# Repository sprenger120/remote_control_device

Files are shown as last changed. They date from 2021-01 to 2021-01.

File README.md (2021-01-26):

# remote_control_device

Firmware, KiCAD files, 3D designes of an embedded STM32 based device I was commissioned to create for an autonomous bike. **Clone with --recursive**
It reads receives stick positions from a hobby remote control (FrSky based) and controls various actors around the bike. Also serves as a CANopen bus master, monitoring for timeouts and handling some safety aspects.   
The firmware is fully unit tested and fuzzed using American Fuzzy Lop. 

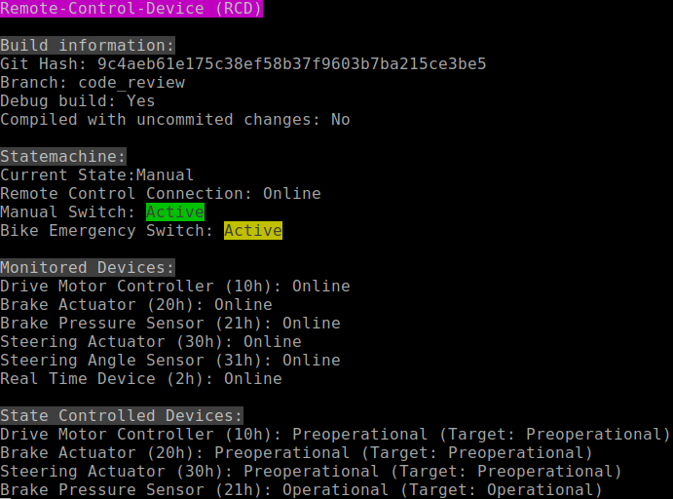
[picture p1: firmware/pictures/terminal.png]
radio front image Serial console


Remote control system for the autonomous bike(s) based on:
 
* FrSky's QX7 remote control
* FrSky's XM+ diversity, non-telemetry receiver
* OpenTX remote control firmware
* ST's NUCLEO-F302R8 board
* custom adapter board
* CANfestival CANopen stack
* STM32 Cube HAL 
* FreeRTOS 

### Project overview / folder stucture
<pre>
remote_control
|-- hardware*          **General information and assembly instructions**
|   |-- 3D             3D models of the units case
|   |-- datasheets     all relevant datasheets of components used in the custom adapter board
|   |-- adapterBoard   KiCAD 5 files
|   |   |-- bom        Interactive BOM for PCB assembly
|-- firmware*          **Code for the micro controller**
</pre>
\* contains extra readme

### General usage of remote control (radio)

Switch on the remote control by holding the center button for 2 seconds. The remote control device in the bike will be in *start* mode until radio link is engaged and all canbus devices area ready. Beware that getting **too close** to the antennas of the RDC with the radio will cause it to loose connection due to overload (the receiver is very sensitive).
The radio will start beeping if left untouched for more than 60 minutes or if the batteries get low. It will never shut off by itself and **will** kill the batteries if signals are ignored.   

To enable any mode the safety switch (momentary - will return to by it's own to default position) has to be flipped up **before** activating either of the two mode switches.
Remote mode will not activate if the throttle is raised. If two modes are activated at the same none will activate.

Emergency can be pressed at at any time. When inside remote or autonomous all switches have to be returned to idle to
leave emergency. Emergency will only be active for the duration of the button press when bike is idling.   

Manual mode overrides **all** control of the bike; even emergency. When exiting manual the bike will not be directly returning to the previous mode.  

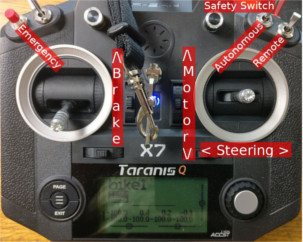
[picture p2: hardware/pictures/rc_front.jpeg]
radio front image


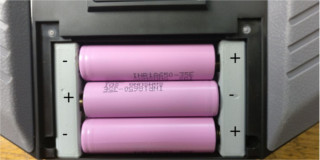
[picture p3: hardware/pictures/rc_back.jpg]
radio back image


### Remote control device LED codes
The LEDs of the device can be in the following states

- off/dim
- fast blinking
- on
- counting (blinking for *n* cycles, off for longer time, repeating)

##### Hardware LED

- off/dim: device is starting
- fast blinking:
    waiting for all canfestival nodes to start up
    no actor values will be sent until this is done
- on: (no errors)
- counting mode:
    - lower counts overwrite higher ones (lower = more important error)
    - 1 count: can network error
    - 2 count: brake heartbeat timeout
    - 3 count: steering timeout
    - 4 count: wheel motor timeout

##### Remote LED

- on: remote control connection established (no errors)
- fast blinking: manual mode (overwrites connection lost / established)
- off: connection lost

### Wiring of remote control device
Input voltage 6-24V (reverse polarity protected) or USB powered through nucleo. ESD protection only rudimentary due to layout error. 
Do not power up device without antennas attached it may shorten the lifespan of the receiver. Switch 01 = manual mode. Switch 02 = hard emergency. Just connect a switch, pull-up is provided by the board.

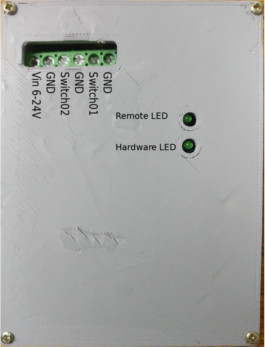
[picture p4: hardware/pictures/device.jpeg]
unit image


## Device pictures

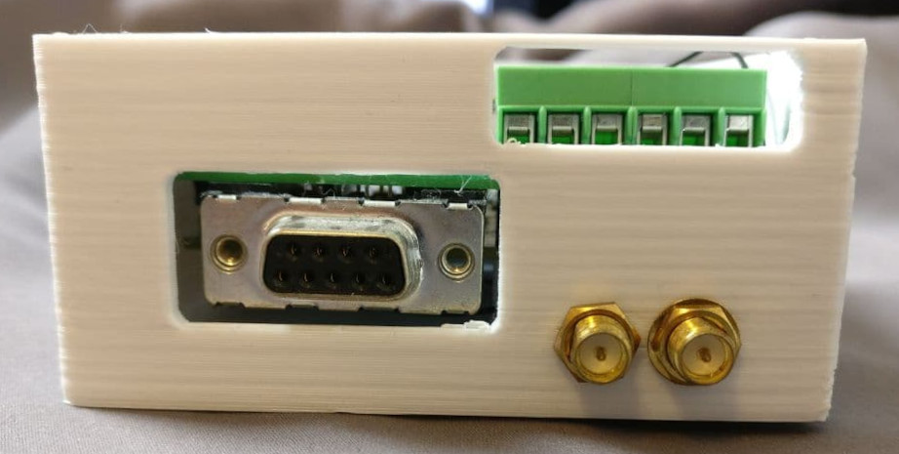
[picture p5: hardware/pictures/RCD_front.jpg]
front image


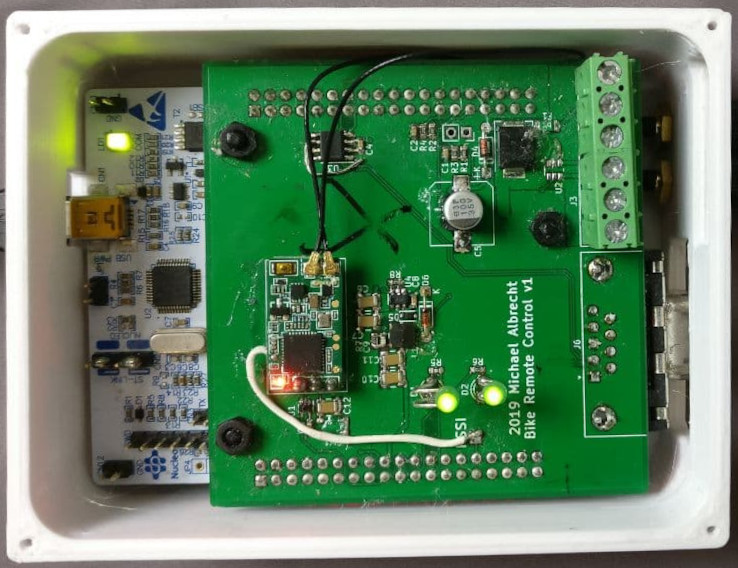
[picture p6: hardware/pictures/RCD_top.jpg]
top without lid


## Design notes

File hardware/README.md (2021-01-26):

# Hardware
- NUCLEO-64 with STM32F302R8 processor with a custom adapter board ontop 
- FrSky XM+ receiver module soldered to the adapter board
- FrSky QX7 remote control with custom emergency stop button and LiIon batteries
- Designed with KiCad 5

### Configuration of remote control
Settings applied to the remote control. You may use OpenTX Companion to copy the config from one radio to the next.

Radio Setup:

- set date, time
- set batt range 9,9-12.6
- batt low warning 10v
- inactivity 60min
- backlight mode: keys
- global functions:
  - 01: on, volume, Input11(s1), active

Setup:

- model name: bike 1
 - s-warning: a,b deactivated
 - internal rf
   - d16
   - ch1-16
   - rx num 1
   - binding:  ch1-8 telem on
   - failsafe: no pulses
- inputs: T, A, E, R, SA, SB, SC, SD, SH, SF, S1, S2, MAX, MAX, MAX, MAX
 - SA input weight -100, offset -100
- mixer click every entry once to assign input
- logical switches
  - 01: a>x, SC, -50
  - 02: a>x, SD, -50
  - 03: AND, L01, L02
- special functions:
  - 01: L03, play sound, wrn1, 1 
  - 02: SA half, play sound, wrn2, -

### Modification of remote control
Opened the unit and removed switch SA and replaced it with a pushbutton. Original hole needs to be enlarged with a drill.

### adapterBoard v1 PCB  Notes
- Buck converter feedback resistive divider component R7 should be 52.3K instead of 52.3R (installed 51K as substitute), corrected in schematic
- XM+ receiver power switch is correctly denoted as normally closed, normally open was accidentally bought, removed SW1 and bridged pads so receiver is always on
- 10uF MLCC were specified as 1210 (imp.) components, 1206 (imp.) were bought, installed 1206 components without issue
- D-SUB connector needs to be soldered to bottom layer because of accidental pinout mirroring
- Modifications to Nucleo board so PCB fits ontop for soldering
   - Snip off Arduino headers on both sides
   - Remove User and Reset button caps and snip button stem even with button casing 
   - Snip off two pin header with jumpers and solder bridges so originl configuration with jumpers is estabilished
- "debugUART" (USART1) and XM+ USART (USART2) need to be switched because the built-in STLinks UART converter is connected to USART2
to achive this the following was done
  - SB14, SB13 resistors have been removed
  - wiring from USART1's pins has been added to the STLinks side of the resistors
- Removed U2 as it is used incorrectly and bridges SW01 and SW02

### Assembly
- assemble adapter board according to interactive bom in adapterBoard/bom
- don't forget to do the buck converter and switch fixes mentioned above
- solder on the XM+ with the help of 3x1 Dupont pin header
- remove original antennas very carefully (do not pull straight up but use a lever below the crimp to pry it off)
- attach the two MHF4 -> RP-SMA adapter cables
- 3D print enclosure (3D folder, [online cad](https://cad.onshape.com/documents/3ef6522cbbdee6598b7177e3/w/a3b5db2935905c5482c54099/e/5c57edc258b28d56febac476)) 
- do modifications to the nucleo board as seen above
- slot adapter board onto nucleo and use nylon standoff to reeinforce connection between the two boards
- screw in the RP-SMA terminals while only using the plain washer but not the split ring
- insert the board into the enclosure and use three M3 screws with appropriate length (25mm) to fasten the board stack to the enclosure
- fasten the enclosure's top with small short wood screws
- flash the latest firmware

### External resources other than datasheets
* [ST Nucleo64 footprint](https://github.com/mobilinkd/stm-morpho-template)

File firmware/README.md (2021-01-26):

### Specific Documentation

- [CanFestival usage](firmware/doc/CanFestivalNotes.md)
- [Software Structure](firmware/doc/Structure.md)
- [Testing methodology](firmware/doc/TestingNotes.md)

### How to change object dictionary

Canfestival brings its own OD editor. The software requires Python 2 and wxgtk (sudo apt install python-wxgtk3.0-dev). Start program with

```bash
python2 ./src/canfestival/objdictgen/objectdictedit.py
``` 

You can now open *./objectDictionary/RemoteControlDevice.od* and start editing it to your liking. 
To apply changes just save the .od file and execute make. The code is automatically generated. 
Be careful as some tests are brittle any may require changing. Also make sure you see the notes in src/CanFestival/CanFestivalLocker.cpp.  
When **changing Heartbeat Consumers** please keep it in sync with src/Statemachine/Canopen.cpp

### Object dictionary configuration
- Based off of configuraition from 2020-12-07
- Node Id: 01h
- Manufacturer Specific 2000h - 5FFFh
  - 2000h: WheelTargetTorque (MCA_M_soll)
  - 2001h: BrakeTargetForce (MCB_F_soll)
  - 2002h: SteeringTargetAngle (MCL_delta_soll)
  - 2003h: SelfState 
  - 2004h: RTD_State
  - 2005h: BikeEmergency (not currently used)
- TPDO Mappings, Transmit parameters:
  - TPDO1: {SelfState}, COB: 181h, EventTime: 100ms (10Hz)
  - TPDO2: {BrakeTargetForce}, COB: 220h, EventTime: 20ms (50Hz)    
  - TPDO3: {SteeringTargetAngle}, COB: 230h, EventTime: 20ms (50Hz)    
  - TPDO4: {WheelTargetTorque}, COB: 210h, EventTime: 20ms (50Hz)  
  - TPDO5: {WheelTargetTorque, BrakeTargetForce, SteeringTargetAngle}, COB 200h, EventTime: 20ms (50Hz)
  - Every PDO's transmission type is "manufacturer specific (0xFE)" with an inhibit time of 0
  - Statemachine runs a 50Hz loop and transmits every cycle in remote mode
- RPDO Mappings, Receive parameters
  - RPDO1: {RTD_State}, COB: 182h, Event Time: 125ms (8Hz)
- Heartbeat Producer with 10Hz
- Heartbeat Consumer 
  - 10h Wheel Motor Controller, Timeout after 500ms
  - 20h Brake Actuator, Timeout after 500ms
  - 30h Steering Actuator, Timeout after 500ms
  - 21h Brake Pressure Sensor, Timeout after 500ms
  - 31h Steering Angle Sensor, Timeout after 500ms
- SDO Parameters
  - SDO Client to Brake Actuator and Steering Actuator

### Compile environment (Linux)

Use the CI artifacts for slow but easiest way to build the firmware. If you want to build locally install

```bash
sudo apt-get install binutils-arm-none-eabi build-essential gcc-arm-none-eabi git python2 bear
```

Please make sure your *arm-none-eabi-gcc* is at least version 9 or else C++17 features used are not available. Also the old compilers won't generate small enough code to fit the FLASH memory of the chip.

```bash
# >=9
arm-none-eabi-gcc --version 
```

If your compiler is too old get **purge the old gcc-arm-none-eabi installation** and get [9-2020-q2-update for x86-64 Linux](https://developer.arm.com/tools-and-software/open-source-software/developer-tools/gnu-toolchain/gnu-rm/downloads). Extract it to somewhere of your liking and edit your ~/.bashrc and add the compiler path to your PATH variable

```bash
# example
PATH=$PATH:/home/micha/Tools/gcc-arm-none-eabi-9-2020-q2-update/bin
```

### Compile environment (Windows)

Good luck! Get MinGW for make and git. Get [9-2020-q2-update for Windows](https://developer.arm.com/tools-and-software/open-source-software/developer-tools/gnu-toolchain/gnu-rm/downloads). That should get you close.

### Compiling 

*Assuming your terminal is in the folder of this document*

```
make -j8 RELEASE=1 RELEASE_OPT=s 
``` 

Your binary is located in the build/release folder.

### How to flash (Linux)

Freshly bought boards have ST-Link as programmer firmware but I've changed it to Segger JLink (see Development (Linux)). Install "JLink Toolchain for Linux" and execute the following command to flash the firmware.

```bash
make RELEASE=1 RELEASE_OPT=s jflash
```

### How to flash (Windows)

Compile the firmware and use the [Windows JLink](https://www.segger.com/downloads/jlink/JLink_Windows.exe).

### Serial  debug 

Connect the NUCLEO board as shown in the previous chapter. Install a serial monitor (gtkterm for Linux, PuTTY for Windows). The board will show as a /dev/ttyACMx / COMx. Use 115200-8-N-1 configuration You will now receive debug output. 

### Development (Linux)

Use [Visual Studio **Code**](https://code.visualstudio.com/). The project is configurated to work nicely with it. Install the recommended extensions. Compiling is done with Ctrl + Shift + B. Use F5 to flash and debug. You'll need to install *gdb-multiarch* and create a link. 

```bash
sudo ln -s /usr/bin/gdb-multiarch /usr/bin/arm-none-eabi-gdb
```

The standard flash / debug device on the NUCLEO boards is not smart enough to be aware of any realtime OS; so only one thread is shown. For a better experience install the [JLink Toolchain for Linux](https://www.segger.com/downloads/jlink/JLink_Linux_x86_64.deb) and change the NUCLEO's debugger's firmware to JLink with [this Tool](https://www.segger.com/products/debug-probes/j-link/models/other-j-links/st-link-on-board/). Remember to also chage the default Run Taks to "Debug (J-Link, RTOS-aware)".

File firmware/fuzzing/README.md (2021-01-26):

# Fuzzing 

Fuzzing is the process of testing an application by strategically modifiying some known good input in order 
to find crashes. This process takes a very long time and it is usually recommended to let your application 
be fuzzed for a week. This setup is using AFL (americal fuzzy lop) to test the firmware. 

### Prerequesites

Install *afl++*, *build-essential*, *g++*, *cmake*, *screen*. Navigate into AFL and execute *make* and *sudo make install*. Navigate into *libdislocator* and *make* it aswell.
Copy the path of *libdislocator.so* into *process/startFuzzing.sh* and change up *AFL_PRELOAD*. Also setup the *MaxCoreCnt* variable with your thread count. For multi cpu machines it may be faster to not go all the way with the core count. Check with *afl-whatsup* if the execs/sec increase or decrease with higher counts.

### Running 

Create a folder *findings_ram*. Initialize a ramdisk in it. 

```
sudo mount -t tmpfs none ./findings_ram
```

Be sure to back up findings_ram every so often when the server is not powered through a USP.

Start *process/startFuzzing.sh*. You can stop all instances with *process/stopFuzzing.sh*. Inspect instances with *screen -r fuzzer[Number]*

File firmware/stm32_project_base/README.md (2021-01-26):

# bus-node-base

This repository contains the build system and common libraries required by all UAVCAN bus nodes.

The following libraries/components are included:
* [libuavcan](https://github.com/UAVCAN/libuavcan)
* [libuavcan STM32 driver](https://github.com/UAVCAN/platform_specific_components/tree/4e0a24756090d218b469f561d7e0d35e5f2f5427)
* [Tracealyzer for FreeRTOS](https://percepio.com/tz/freertostrace/)

## Prequisites

### [GNU Arm Embedded Toolchain (arm-none-eabi)](https://developer.arm.com/tools-and-software/open-source-software/developer-tools/gnu-toolchain/gnu-rm/downloads)

In order for bus-node-base to be compilable, it requires at minimum a version of the GNU Arm Embedded Toolchain that supports C++17. You should, however, stick to the latest version if possible.

**DO NOT** install the toolchain via *apt* from the Ubuntu archives or a PPA, as these sources usually provide very outdated versions.

1. Goto the download site and download the Linux x86_64 Tarball.
2. Extract the files to the target install directory, e.g. by `$ cd $install_dir && tar xjf gcc-arm-none-eabi-*-yyyymmdd-linux.tar.bz2`
3. Add the bin directory permanently to your PATH environment variable using the following commands:

  ```
  $ export PATH=$PATH:$install_dir/gcc-arm-none-eabi-*/bin
  $ arm-none-eabi-gcc
  ```

  If you are using Ubuntu, have a look at [this](https://help.ubuntu.com/community/EnvironmentVariables) to select an appropriate location for the script so it will either affect all shells of a particular user or the entire system.

You should also have a look at the file `share/doc/gcc-arm-none-eabi/readme.txt` which contains additional information about installation and usage.

### [Visual Studio Code](https://code.visualstudio.com/)

You can, of course, choose any code (or even plain text) editor for programming the UAVCAN nodes, but VS Code makes the whole edit-compile-debug cycle much more comfortable. It incorporates git, the possibility to configure multiple launch and debug targets, debugging support for Cortex-M targets (via plugins) and is overall highly customizable, so I *really* recommend its utilization.

1. Download the .deb package (it does not matter wether you choose the default one or the Insiders Edition) from the official site. Alternatively, you can install it via snap by running `sudo snap install code --classic` or `sudo snap install code-insiders --classic` from a terminal.

2. Now open VS Code and open the extensions tab (either by clicking on the icon on the leftmost bar or by pressing *Ctrl+Shift+X*). Search for the following extension IDs and add them by clicking *Install*:
   
  | Name | Extension ID | Description |
  | - | - | - |
  | [ARM](https://marketplace.visualstudio.com/items?itemName=dan-c-underwood.arm) | dan-c-underwood.arm | Language support for ARM assembly |
  | [C/C++](https://marketplace.visualstudio.com/items?itemName=ms-vscode.cpptools) | ms-vscode.cpptools | C/C++ IntelliSense, debugging, and code browsing |
  | [Cortex-Debug](https://marketplace.visualstudio.com/items?itemName=marus25.cortex-debug) | marus25.cortex-debug | ARM Cortex-M GDB Debugger support for VSCode |
  | [Cortex-Debug: Device Support Pack - STM32F1](https://marketplace.visualstudio.com/items?itemName=marus25.cortex-debug-dp-stm32f1) | marus25.cortex-debug-dp-stm32f1 | SVD definitions for Cortex-Debug for viewing peripheral registers of STM32F1 devices |
  | [Cortex-Debug: Device Support Pack - STM32F4](https://marketplace.visualstudio.com/items?itemName=marus25.cortex-debug-dp-stm32f4) | marus25.cortex-debug-dp-stm32f4 | SVD definitions for Cortex-Debug for viewing peripheral registers of STM32F4 devices |
  | [LinkerScript](https://marketplace.visualstudio.com/items?itemName=zixuanwang.linkerscript) | zixuanwang.linkerscript | Language support for GNU linker script |

### [CubeMX](https://www.st.com/en/development-tools/stm32cubemx.html)

CubeMX is a graphic tool developed by ST that allows you to configure STM32 microcontrollers easily. It generates C initialization code based on the chosen peripherals and automatically adds the required drivers from the STM32CubeHAL. While it still has some bugs that require attention, this tool is a very valuable tool that simplifies the configuration process a lot compared to writing all the initialization code by hand.

Download the tool from ST's website. Unpack the ZIP file and run the `SetupSTM32CubeMX-x.x.x.linux` file.

### [J-Link Software and Documentation Pack](https://www.segger.com/downloads/jlink/#J-LinkSoftwareAndDocumentationPack)

We primarily use the [J-Link EDU](https://www.segger.com/products/debug-probes/j-link/models/j-link-edu/) debug probe for flashing and debugging our microcontroller targets. To be able to use it, you have to download the [J-Link Software and Documentation Pack](https://www.segger.com/downloads/jlink/#J-LinkSoftwareAndDocumentationPack) (direct [link](https://www.segger.com/downloads/jlink/JLink_Linux_x86_64.deb) for the 64-bit DEB installer) and install it.

### [Tracealyzer](https://percepio.com/tracealyzer/)

The Tracealyzer is a tool for monitoring various FreeRTOS-related diagnostics, such as tasks and their states, heap and stack usage, kernel objects etc. While its usage is not mandatory, it is absolutely recommended because otherwise you will often end up making blind guesses about what caused your RTOS to stall.

As this software requires a license key and only allows a limited number of installations, contact the team leader for the installation package and license key.

After extraction, read `RunningOnLinux.txt` **carefully**. Especially pay attention to the **SEGGER J-Link support** section at the end of the file or otherwise Tracealyzer will not recognize the J-Link probe.

## Project setup

In order to create a new bus node running UAVCAN, you need to create an empty repository and add this one as a submodule. Run `git submodule update --init --recursive` to properly initialize the nested submodules. Afterwards, add a *Makefile* that looks like the following:

```make
TARGET  := example-node
RTOS    := freertos
DEVICE  := stm32f103re

UAVCAN_STM32_TIMER_NUMBER   := 7
UAVCAN_STM32_NUM_IFACES     := 1

STM32_PCLK1     := 42000000
STM32_TIMCLK1   := 84000000

INCDIRS         := include/
SOURCES         := src/main.cpp

# Actual build engine
include bus-node-base/include.mk
```

| Parameter | Meaning |
| - | - |
| `TARGET` | The name of the resulting firmware image (without extension) |
| `RTOS` | Can be one of the following:<ul><li>`none` There is no OS being used</li><li>`freertos` FreeRTOS is being used</li></ul> |
| `DEVICE` | Device identifier of your target MCU, e.g. `stm32f103re`. Can be omitted if you do not intend to flash using a J-Link from a command line. |
| `UAVCAN_STM32_TIMER_NUMBER` | The number of the hardware timer used for clock functions. Consider using a *basic timer* (see the [STM32 timers](#stm32-timers) section below). |
| `UAVCAN_STM32_NUM_IFACES` | The number of CAN interfaces that will be used (some have two). Defaults to 1 if not specified. |
| `STM32_PCLK1` | PCLK1 (APB1) frequency in Hertz (see [clock configuration](#clock-configuration)) |
| `STM32_TIMCLK1` | TIMCLK1 frequency in Hertz (see [clock configuration](#clock-configuration)) |
| `INCDIRS` | List of include directories |
| `SOURCES` | List of application source files to be compiled |
| `UAVCAN_MEMPOOL_SIZE` | *optional* Memory pool size for internal uavcan allocations. Default 16KiB |
| `UAVCAN_RX_QUEUE_SIZE` | *optional* RX queu size. Hard minimum is 10. Default 128 |
| `TRACEALYZER_SUPPORT` | *optional* Enabled / Disables Tracealyzer. Default enabled |

Also add a `.gitignore` file. Just copy `bus-node-base/templates/gitignore` to the project root and prefix its filename with a dot (`.`).

## CubeMX setup

Now you need to create a new CubeMX project. To do so, open the application and click *File > New project ...* or hit *Ctrl+N*. Select the MCU and the package you are going to use and then click *Start Project* on top of the page.

Follow the instructions below **in the order they are listed**. The headlines correspond to the tabs in the project window.

### Project manager

#### Project

* Change the Application Structure to **Advanced**.
* Select **Makefile** as the Toolchain / IDE.
* Ignore all "Empty project name" errors and check if the settings stuck after saving the project.

#### Code Generator

* Select **Copy only the necessary library files**. Otherwise you end up having more than 100 MiB to upload.
* Check **Generate peripheral initialization as a pair of .c/.h files per peripheral**.
* Enable **Set all free pins as analog**.
* If you want, check *Enable Full Assert*.

Now save the project by clicking *File > Save Project As ..* or by hitting *Ctrl+A*. You will have to choose a folder as the location for the project, so create a new sub-directory in the project directory called *TARGET.cubemx*, where *TARGET* corresponds to the variable you defined earlier in the Makefile. So in the example above our folder would be named *example-node.cubemx*.

### Pinout and configuration

1. Goto *System Core > RCC*. Select **Crystal/Ceramic Resonator** for the High Speed Clock (HSE).
2. Goto *System Core > SYS*. Select **Trace Asynchronous Sw** as the debug interface.
3. Activate and configure all peripherals you want to use.
4. You especially need to enable **CAN** (or **CAN1** if your MCU has multiple CAN controllers). Further setup of the CAN peripheral is not required, as this will be done by the libuavcan driver.

#### When using FreeRTOS

1. Goto *Middleware > FREERTOS > Mode* and select **CMSIS_V2** as the interface.
2. Under *Configuration > Config parameters* configure FreeRTOS as desired.
    * Enable **RECORD_STACK_HIGH_ADDRESS** to ease debugging issues related to stack overflows.
    * Pay attention to **TOTAL_HEAP_SIZE** as this value is most likely way to small and prevents you from choosing an appropriate task stack size later on.
    * Select **heap_1** as the memory management scheme.
    * Choose **Option2** for **CHECK_FOR_STACK_OVERFLOW**.
    * Make sure that **USE_TRACE_FACILITY** is **enabled**, otherwise the firmware can't interact with the Tracealyzer. Leave disabled when Tracealyzer support is not required.
3. Next, on the *Tasks and Queues* tab, create the individual tasks and queues as necessary.
    * Note that the default task **cannot** be deleted and that the Code Generation Option **must** be *Default*. Renaming, however, is possible.
    * If you want to define your tasks outside the generated *main.c*, choose *External* for the Code Generation Option. *Keep in mind that you will have to define your task function as `extern "C"` when defining them in a C++ source file.*
4. Goto *System Core > SYS > Mode* and change the *Timebase Source* to a timer **different from SysTick and the timer chosen for UAVCAN** (see Makefile options and the [STM32 timers](#stm32-timers) section below).
5. Goto *System Core > NVIC > Configuration* and tick for each interrupt service routine that shall be able to use the FreeRTOS API the corresponding checkbox in the *Use FreeRTOS functions* column. **Violating this rule will have CubeMX assign wrong interrupt priorities resulting in a hard fault eventually.**

### Clock configuration

While the view in this section very much depends on your MCU, there are a few things that should always be done here.

1. Enter the frequency of the HSE crystal in use.
2. Select **HSE** as the source of the PLL.
3. Make sure the system clock MUX uses **PLLCLK** as its input.
4. Enter your desired system clock (HCLK).
5. Only alter the peripheral clock settings if you have special requirements.
6. If there are any red fields in the clock tree, click 'Resolve Clock Issues' on the top of the page.
7. Note down the **APB1 peripheral clocks** and **APB1 Timer clocks** values; they are required in the project's Makefile (see above).

## First-time code generation

When you are done configuring the CubeMX project, click *GENERATE CODE* at the top of the page. CubeMX will display a warning message if there is anything misconfigured. When the process has finished, you have to make some minor addittions to the generated files.

### Makefile

Go to the *.cubemx* sub-directory and open the *Makefile* in an editor. Delete everything except the following variables/sections:

* C_SOURCES
* ASM_SOURCES
* CPU
* FPU
* FLOAT_ABI
* MCU
* AS_DEFS
* C_DEFS
* AS_INCLUDES
* C_INCLUDES
* LDSCRIPT
* **The EOF marker at the end of the file**

### Chip definitions

You need to provide a file called `chip.h` that includes the HAL file for the MCU and defines the names of the interrupt service routines for the CAN driver. The file will be used by the UAVCAN driver and the Tracealyzer.

Implementations for *STM32F1* and *STM32F4* series chips are already in the include path. If you use another MCU take a look at *chip/chip.h*.

### Tracealyzer support

**Skip this step when no Tracealyzer support is required.** 
Open *.cubemx/Core/Inc/FreeRTOSConfig.h* and head for the end of the file. Include the the Tracealyzer header in the user code section like the follwing:

```C
/* USER CODE BEGIN Defines */
#include "trcRecorder.h"
/* USER CODE END Defines */
```

This changes will not be overridden when re-generating the code.

## Visual Studio Code configuration

### Include paths and preprocessor definitions

1. If not already present, create a directory called `.vscode` in you project's root directory.
2. Copy `bus-node-base/templates/c_cpp_properties.json` into said directory.
3. Adjust the configuration to your needs.
  * Add the include paths listed under *C_INCLUDES* in `*.cubemx/Makefile`. Most are platform-specific and are thus not part of the template.
  * Add the include path for the *chip.h*
  * Add all of your own include paths
  * Provide a proper definition for your MCU family

### Launch configurations

Just copy `bus-node-base/templates/launch.json` to `.vscode/`. This default launch set contains three configurations, one for the J-Link probe without an RTOS being used, another one for the J-Link with FreeRTOS running and one for an ST-LINK device (available on ST's nucleo boards, without using an RTOS).

Foreach configuration you have to adjust some attributes:
* `executable`: Insert the correct name of the TARGET
* `device`: The actuel part number of the MCU, e.g. *STM32F103RE*

For some MCUs of the STM32F1 and STM32F4 families there are peripheral register definitions (SVD files) available through the two Device Support Packs you installed earlier. In this case setting the `device` attribute is sufficient. However, if your MCU is not covered (see [Debugging](#debugging) section on how to find out), you will have to provide an SVD file on your own, just search for it on [ST's website](https://www.st.com/content/st_com/en.html). Put the file somewhere in your project directory and add an `svdFile` attribute like the following:
```json
"svdFile": "{workspaceRoot}/STM32F446.svd"
```

### Build tasks

Lastly, copy `bus-node-base/templates/tasks.json` to `.vscode/`. This file contains four different build tasks:

| Task | Decription |
| - | - |
| Clean all | Deletes the entire *build* directory |
| Build firmware (Debug) | Creates a debug build, which is task run most often. Can be run by *Ctrl+Shift+B* |
| Build firmware (Release) | Creates a release build with `-O3` option |
| Build firmware (Release, size-optimized) | Creates a release build with `-Os` option |

## Building

* **From within Visual Studio Code**

  To build the firmware in debug mode just press *Ctrl+Shift+B*. To clean up or do a release build, run the corresponding task via the *Tasks: Run Task* command from the command palette.

* **Externally (shell)**

  You just need to run `make` inside your project's root directory for the debug build. For the release build, append `RELEASE=1` and optionally `RELEASE_OPT=x`, where *x* is a valid GCC optimization option, like `3` or `s`.
  
  To remove all build-related files run `make clean`.

The resulting firmware image can be found in `<your-project>/build/{debug,release}/<TARGET>.bin`. If anything goes wrong, see the [Known issues](#known-issues) section below.

## Flashing via command line

Flashing via the command line takes some additional steps. If you start debugging from Visual Studio Code you can skip this section since the target MCU will be flashed automatically by the debug task.

* via *ST-LINK*

  Run `make stflash` for the debug build. Append `RELEASE=1` for the release build.

* via *J-Link*

  If you are flashing for the first time, you need to to copy `bus-node-base/templates/flash_commands.jlink` to the project's root directory and modify it. In the second line adjust the name of your target binary, e.e. `example-node.bin`. Also make sure to have included a definition for `DEVICE` in your Makefile.

  After that and each subsequent time, run `make jflash`.

  **NOTE:** You cannot switch between debug/release easily. This command always uploads the file you specified in *flash_commands.jlink*.

## Debugging

*This section is yet to be written.*

## Known issues

### Multiple defintition of 'SysTick_Handler'

**Do not comment out this line when tracealyzer is disabled!**  
Including the Tracealyzer headers currently results in compilation errors since the *SysTick_Handler* will be defined twice. To fix this, open *.cubemx/Core/Inc/FreeRTOSConfig.h* and head for the end of the file. Search for the following line:

```C
#define xPortSysTickHandler SysTick_Handler
```

Comment this line out.

Unfortunately this line is not in a user code section and thus **needs to be commented out each time the code is re-generated**.

### Duplicate lines in the CubeMX Makefile

Whenever you re-generate the code using CubeMX, it will adjust the Makefile in the sub-directory by updating sources and include paths. Sometimes it inserts a duplicate of the last line of either of these resulting in syntax errors. In this case, just remove the duplicate lines.

### make: *** No rule to make target needed by 'all'.  Stop.

You have declared files in INCDIRS or SOURCES that don't exist.

### Firmware immediately jumps into defaultHandler when Tracealyzer is disabled.

FreeRTOS doesn't have its SysTick_Handler linked. Do not remove the #define generated by CubeMX.

## Additional notes

### STM32 timers

bus-node-base requires 3 different timers for the following components:

* **The FreeRTOS scheduler**

  The scheduler's tick function must be called at an regular interval (by default 1000 Hz) to be able to switch contexts. The **SysTick** timer was designed specifically for that purpose, so if you activate FreeRTOS within CubeMX the SysTick timer will automatically be used as the tick source.

* **STM32CubeHAL**

  The CubeHAL requires the use of a timer for timeout detection. When not using FreeRTOS this is the SysTick timer by default. When using it, you can choose any other timer for this purpose, but make sure it is not the same timer used for the UAVCAN driver. Consider using a **basic timer** if available.

* **UAVCAN driver**

  The UAVCAN driver uses a timer for clock functions. You can choose any timer connected to *APB1* other than the one used by CubeHAL for this purpose. Consider using a **basic timer** if available.

See [AN4013](https://www.st.com/resource/en/application_note/dm00042534-stm32-crossseries-timer-overview-stmicroelectronics.pdf) for an overview of the various kinds of timers used in STM32 microcontrollers and specific timer numbers and types in the device families.

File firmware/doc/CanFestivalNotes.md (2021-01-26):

# Notes on canfestival usage/changes in this project

### Linking, Including

Canfestival is designed to be either linked statically for embedded devices or dynamically for everything else. 
I chose not to use the supplied build system as its quicker to just create a quick Makefile include (canfestival/canfestival.mk) 
and add the library directly.
This poses some challenges as all the includes are not prefixed by e.g. canfestival so there are conflicts with the CubeMX generated code 
under remote_control_device.cubemx. I've changed all includes inside the library to point to canfestival/...h.  

### Driver 

The library also comes with driver code even with CMSIS compatible ones. As CubeMX auto generates setup code for the CAN device, 
using the canfestival driver code would be redundant. All I have to add some small functions for sending.

### Scheduling / Timers

Inside the library there is a micro scheduler for timed events that just uses a hardware timer's interrupt. This is problematic
in this project as I'm using an RTOS and canfestival is not thread safe (+ you can't aquire mutexes inside an interrupt). 
I've replaced the whole subsystem with the canFestivalTimer task.

### Configuration

Canfestival requires four configuration files to work. These have been copied from multiple places of the library and modified to 
suit the needs of the project. You can find them in src/canfestival_config/canfestival/*.h

### objdictgen

CANopen nodes require an object dictionary and canfestival brings and editor (objdictedit.py) and a code generator for .c/.h files (objdictgen.py).
The library is somewhat old and these programms are written with python 2 and might be hard to run later.   

objdictgen.py only requires the gnosis xml parser to run. As pip is removing support for python2 soon I've added the complete library for 
"future-proofing" at least this part. Python2 itself should be available at least for some time more.   

objdictedit.py is trickier as it requires wxPython which itself is a wrapper for some gui stuff. As long as wx has python2 support there should be
no problem. It might be required to port it though.

### Testing

There are some tests supplied with the library to ensure basic functionality. gTest is used and can be installed with your favorite packet manager. 
HippoMock used to be retrieved with a power shell script. To avoid this nonsense I've added the framework directly.

I've also added a CMake configuration to build the test app. As I'm not using the drivers of the library I also needed to add some
empty functions so the linker is satisfied and HippoMock can work its magic.  

Testing will be done with gitlab CI

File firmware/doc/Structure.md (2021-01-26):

### Code overview

<pre>
├── base
├── canfestival
├── hippomocks
├── objectDictionary
│   ├── generatedOD
│   └── RemoteControlDevice.od
├── remote_control_device.cubemx
├── src
│   ├── CanFestival
│   ├── PeripheralDrivers
│   ├── Statemachine
│   ├── *
</pre>

- base: Makefile build engine, C++ embedded bindings, git information retrieval
- canfestival: CANopen stack and tests
- hippomocks: Mocking library for CanFestival and firmware
- objectDictionary: CanFestival objgenedit file, generated .c / .h files
- remote_control_device.cubemx: Chip initialisation / HAL code generated by STM32 CubeMX
- src/CanFestival: Support code to make CanFestival usable with modern C++ / RTOS
- src/PeripheralDrivers: RTOS Tasks handling CAN and UARTs
- src/Statemachine: 'Brain' of the application. Binds all parts of the application together
- src/* : Support code / separated out code for better testing 

**See [Structure.pdf](firmware/doc/structure.pdf) for internal data flow.**

### Why a realtime operating system is necessary

For project where you are only doing one thing an RTOS is overkill and a superloop is sufficient.
But as soon as you have to juggle more data sources and calculations / tranmissions have to be done 
one time its hard to justify not using one. An RTOS makes it easy to keep hard realtime constraints with
low jitter as you are encouraged to keep interrupt code short and instead deferr proecessing to a task
which in turn can process when constraints allow it. 

### Application bootup 

1. The chip resets on powerup and begins executing the startup assembly code (remote_control_device.cubemx/startup_stm32f302x8.s) which sets up the interrupt vectors and copies variable's initialisation data into ram.

2. remote_control_device.cubemx/Core/Src/main.c main() is executed which initializes clocks and peripherals, creates tasks (remote_control_device.cubemx/Core/Src/freertos.c) and starts the FreeRTOS scheduler which immediately takes control of the execution flow executing tasks that are in the ready state always preferring higher priority tasks. 

3. The system tick interrupt runs every millisecond (configured in remote_control_device.cubemx/Core/Inc/FreeRTOSConfig.h) allowing the scheduler to interrupt the currently running thread to schedule another one.

### Tasks

Every task has more in depht explaination in their header file. 

- FreeRTOS' Timer Task: runs src/LEDs code at specified intervals depending on the blinking mode
- CanFestivalTimers: src/CanFestival/CanFestivalTimers Executes timers registered by CanFestival 
- ReceiverModule: src/PeripheralDrivers/ReceiverModule Starts / waits for reception of data from FrSky XM+ receiver module. Also decodes data upon arrival.
- CanIO: src/PeripheralDrivers/CanIO handles can peripherals TX / RX mailboxes. Adds send / dispatch hooks for CanFestival communication.
- TerminalIO: src/PeripheralDrivers/TerminalIO debug console, handles UART reception / transmission
- Statemachine: src/Statemachine/Statemachine checks 'StateChangingSources' and switches internal state depending on it. Handles in state operations such as preparing remote control inputs for CanFestival

### General task structure

You can differentiate between "Hardware" and "Software" handling tasks. 

- a Hardware-handling tasks is blocked most of the time waiting for the processor to call an interrupt service routine (ISR) which is bound to a callback within the class. This callback then uses FreeRTOS Notify functions to signal the event, the task is then unblocked.

- a Software-handling task will be executed periodically and employs FreeRTOS vTaskDelay function. 

All tasks are designed to be semi-singletons. Due to testing requirements there had to be some hacking in order to test these things properly.

### Statemachine

The complete behavior of a state is within a Statemachine::State instance. All states are contained in the big Statemachine::_states array. See Statemachine::State doxygen comment about capabilities attributes. Every state requires a priority to retain order when more than one states are available for switching to.  

### Canopen

Interface between the statemachine and CanFestival. The separation is necessary to keep the code readable and testable. Canopen can be tested by itself and statemachine can get a mock of canopen for validation.

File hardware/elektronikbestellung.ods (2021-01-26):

Mfr. Part. No. | Descr. | Volume | Digikey L. | Digikey P. | Mouser L. | Mouser P. | Farnell L. | Farnell P. | conrad l. | conrad p.
mcp16331CH | 50V 500mA buck | 10 | https://www.digikey.de/product-detail/en/microchip-technology/MCP16331T-E-CH/MCP16331T-E-CHCT-ND/4972815 | 12 | https://eu.mouser.com/ProductDetail/Microchip-Technology/MCP16331T-E-CH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 | 11.4 | https://de.farnell.com/microchip/mcp16331t-e-ch/50v-nicht-synch-abw-rtsspannungsregler/dp/2448515?st=mcp16331 | 10.4 | - | -
sn65hvd232 | can driver | 10 | https://www.digikey.de/product-detail/en/texas-instruments/SN65HVD232DR/296-26344-1-ND/2254978 | 16.07 | https://eu.mouser.com/ProductDetail/Texas-Instruments/SN65HVD232DR?qs=sGAEpiMZZMuo%252BmZx5g6tFL5kWJ52EgZi | 14.4 | https://de.farnell.com/texas-instruments/sn65hvd232d/can-transceiver-65hvd232-soic8/dp/1103107?st=sn65hvd232 | 19.6 | - | -
SMCJ26CA | tvs diode 26V | 10 | https://www.digikey.de/product-detail/en/littelfuse-inc/SMCJ26CA/SMCJ26CALFDKR-ND/1817235 | 5.41 | https://eu.mouser.com/ProductDetail/Bourns/SMCJ26CA?qs=sGAEpiMZZMtadyunAd%252B8Z02wvYW6BnQn | 4.24 | https://de.farnell.com/littelfuse/smcj26ca/tvs-diode-1-5kw-26v-bidir-do-214ab/dp/2762836?st=SMCJ26CA | 5.05 | - | -
USBLC6-2SC6 | logic level tvs diode | 10 | https://www.digikey.de/product-detail/en/stmicroelectronics/USBLC6-2SC6/497-5235-1-ND/1121688 | 3.56 | https://eu.mouser.com/ProductDetail/STMicroelectronics/USBLC6-2SC6 | 3.27 | https://de.farnell.com/stmicroelectronics/usblc6-2sc6/esd-schutzdiode-3-5pf-17v-sot23/dp/1269406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 | 3.75 | - | -
LD09S13A4GX00LF | dsub connector 9 pin | 10 | https://www.digikey.de/product-detail/en/amphenol-icc-fci/LD09S13A4GX00LF/609-5189-ND/4997291 | 7.7 | https://eu.mouser.com/ProductDetail/Amphenol-FCI/LD09S13A4GX00LF | 7.1 | https://de.farnell.com/amphenol-icc-fci/ld09s13a4gx00lf/d-sub-conn-rcpt-r-a-9pos-th/dp/2892491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 | 8.57 | - | -
SN74AHC1G04 (http://www.ti.com/general/docs/suppproductinfo.tsp?distId=10) | single inverter | 10 | https://www.digikey.de/product-detail/en/texas-instruments/SN74AHC1G04DCKR/296-1090-6-ND/1849019 | 2.85 | https://eu.mouser.com/ProductDetail/Texas-Instruments/SN74AHC1G04DCKR | 2.52 | https://de.farnell.com/texas-instruments/sn74ahc1g04dckr/ic-inverter-gatter-1fach-smd-gz/dp/2436814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 | 2.87 | - | -
151031VS06000 | green led through hole | 50 | https://www.digikey.de/product-detail/en/wurth-electronics-inc/151031VS06000/732-5008-ND/4489988 | 6.73 | https://eu.mouser.com/ProductDetail/Wurth-Elektronik/151031VS06000 | 6.3 | https://de.farnell.com/wurth-elektronik/151031vs06000/led-3mm-blaugr-n-20mcd-568nm/dp/2322130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 | 7.4 | - | -
1935200 | screw terminal | 10 | https://www.digikey.de/product-detail/en/phoenix-contact/1935200/277-1581-ND/568618 | 10.51 | https://eu.mouser.com/ProductDetail/Phoenix-Contact/1935200?qs=sGAEpiMZZMuVJC7Vq%252BMl50V1x%2FrGxbyQ | 10.2 | https://de.farnell.com/phoenix-contact/pt1-5-6-5-0-h/anschl-blck-pcb-schraub-5-0mm/dp/1793679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 | 10.2 | - | -
 | pptc fuse 100mA 1206 | 50 | https://www.digikey.de/product-detail/en/bel-fuse-inc/0ZCJ0010FF2E/507-1794-1-ND/4156222 | 4.97 | https://eu.mouser.com/ProductDetail/Bel-Fuse/0ZCJ0012FF2E | 4.25 | https://de.farnell.com/multicomp/mc36204/ptc-sicherung-r-ckst-smd-60v-100ma/dp/1861161RL?st=pptc | 3.57 | - | -
1N4148 | fast switching diode | 100 | https://www.digikey.de/product-detail/en/on-semiconductor/1N4148/1N4148FS-ND/458603 | 2.94 | https://eu.mouser.com/ProductDetail/ON-Semiconductor-Fairchild/1N4148?qs=sGAEpiMZZMudZehw8RjeZWbu6z6oTQTL | 1.8 | https://de.farnell.com/vishay/1n4148-tap/kleinsignaldiode-100v-do204-ah/dp/2889103?st=1n4148 | 4.93 | - | -
 | 100uF 35V polar cap 10x10.5 | 10 | https://www.digikey.de/product-detail/en/panasonic-electronic-components/EEE-FK1J101P/PCE3819CT-ND/766195 | 5.77 | https://eu.mouser.com/ProductDetail/Nichicon/UWT1V101MCL1GS?qs=sGAEpiMZZMtZ1n0r9vR22RxmuzErLMSVBmnA2mTwl6Q%3D | 2.17 | https://de.farnell.com/vishay/mal218097002e3/kondensator-82-f-35v-20-radial/dp/2520816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 | 11.3 | - | -
 | 10uF mlcc 35V 1210 | 100 | https://www.digikey.de/product-detail/en/taiyo-yuden/GMK325BJ106KN-T/587-1439-1-ND/1004070 | 29.91 | https://eu.mouser.com/ProductDetail/Murata-Electronics/GRM319R6YA106MA12D | 12.2 | https://de.farnell.com/taiyo-yuden/gmk325bj106kn-t/kondensator-10-f-35v-10-x5r-1210/dp/1463373?st=mlcc | 33.4 | - | -
 | 100nF mlcc 35V 0603 | 100 | https://www.digikey.de/product-detail/en/taiyo-yuden/GMK107B7104KAHT/587-3354-1-ND/4157241 | 4.92 | https://eu.mouser.com/ProductDetail/Yageo/CC0603JPX7R9BB104 | 2.7 | https://de.farnell.com/avx/06031c104kat2a/kondensator-0-1-f-100v-10-x7r/dp/2749806?st=mlcc | 6.94 | - | -
 | 20pF mlcc 50V NP0 0603 | 100 | https://www.digikey.de/product-detail/en/yageo/CC0603JRNPO9BN200/311-1424-1-ND/2833730 | 1.91 | https://eu.mouser.com/ProductDetail/Yageo/CC0603JRNPO9BN200 | 2.3 | https://de.farnell.com/multicomp/mc0603n200j500ct/kondensator-20pf-50v-5-c0g-np0/dp/2627461?st=mlcc | 3.66 | - | -
 | 100k R 0603 | 100 | https://www.digikey.de/product-detail/en/yageo/RC0603JR-07100KL/311-100KGRCT-ND/729645 | 0.72 | https://eu.mouser.com/ProductDetail/Vishay-Dale/CRCW0603100KFKEAC | 1.1 | https://de.farnell.com/vishay/crcw0603100kfkea/dickschichtwiderstand-100k-1-0/dp/1469649?st=smd%20widerstand | 1.32 | - | -
 | 10k R 1% 0603 | 100 | https://www.digikey.de/product-detail/en/yageo/RC0603FR-0710KL/311-10.0KHRCT-ND/729827 | 0.87 | https://eu.mouser.com/ProductDetail/Vishay-Dale/CRCW060310K0FKEAC | 2.7 | https://de.farnell.com/vishay/crcw060310k0fkea/dickschichtwiderstand-10k-1-0/dp/1469748?st=smd%20widerstand | 1.32 | - | -
 | 52.3R 1% 0603 | 100 | https://www.digikey.de/product-detail/en/yageo/RC0603FR-0752R3L/311-52.3HRDKR-ND/733183 | 0.87 | https://eu.mouser.com/ProductDetail/Yageo/AC0603FR-0752R3L?qs=sGAEpiMZZMu61qfTUdNhG2gsBIEdmNID3bKC9EK4WEc%3D | 0.7 | https://de.farnell.com/multicomp/mcwr06x52r3ftl/dickschichtwiderstand-52r3-1-0/dp/2694892?st=smd%20widerstand | 0.36 | - | -
BAT46WJ | schottky diode 100V 250mA | 10 | https://www.digikey.de/product-detail/en/nexperia-usa-inc/BAT46WJ115/1727-4817-1-ND/2531304 | 2.61 | https://eu.mouser.com/ProductDetail/Nexperia/BAT46WJ115?qs=sGAEpiMZZMvdQ1HW%252BA9zX8g2LC1ty7TH | 2.14 | https://de.farnell.com/nexperia/bat46wj-115/schottky-diode-100v-0-25a-sod323f/dp/1859908?st=BAT46WJ | 2.53 | - | -
NR4018T220M | inductor 22uH 500mA | 10 | https://www.digikey.de/product-detail/en/taiyo-yuden/NR4018T220M/587-1667-1-ND/1008282 | 3.53 | https://eu.mouser.com/ProductDetail/Taiyo-Yuden/NR4018T220M | 1.84 | https://de.farnell.com/bourns/srn4018-220m/inductor-semi-shielded-22uh-900ma/dp/2408940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 | 3.3 | - | -
NUCLEO-F302R8 | stm32 development board | 2 | https://www.digikey.de/products/en?keywords=NUCLEO-F302R8 | 19.6 | https://eu.mouser.com/ProductDetail/STMicroelectronics/NUCLEO-F302R8 | 18.74 | https://de.farnell.com/stmicroelectronics/nucleo-f302r8/nucleo-board-mcu/dp/2424209?st=NUCLEO-F302R8 | 20.18 | - | -
 |  |  |  |  |  |  |  |  | - | -
 | FrSky QX7 remote control | 2 | - | - | - | - | - | - | https://www.conrad.de/de/p/frsky-taranis-q-x7-hand-fernsteuerung-2-4-ghz-anzahl-kanaele-16-1590638.html | 277.3
 | FrSky XM+ receiver | 2 | - | - | - | - | - | - | https://www.conrad.de/de/p/16-kanal-empfaenger-frsky-xm-sbus-2-4-ghz-1590641.html | 38.64
 | Drucktaster | 3 | - | - | - | - | - | - | https://www.conrad.de/de/p/tru-components-tc-r13-24a1-05-rd-drucktaster-250-v-ac-1-5-a-1-x-aus-ein-tastend-1-st-1587869.html | 3.18
 | IPEX MHF4 to RP-SMA adapter | 5 | - | - | - | - | - | - | https://www.conrad.de/de/p/pigtail-kabel-mhf4-rp-sma-rsma-30cm-fuer-m-2-wlan-3g-gps-800408409.html | 14.2
 | 2.4GHz Antennen Verlängerung | 4 | - | - | - | - | - | - | https://www.conrad.de/de/p/digitus-wlan-antennen-verlaengerungskabel-1x-rp-sma-stecker-1x-rp-sma-buchse-1-50-m-schwarz-973986.html | 36.96
 | 18650 LiIon | 6 | - | - | - | - | - | - | https://www.conrad.de/de/p/samsung-inr18650-35e-spezial-akku-18650-hochstromfaehig-flat-top-li-ion-3-6-v-3450-mah-1499572.html | 44.34
 | Fenix ARE-C2 LiPo x4 Ladegerät | 1 | - | - | - | - | - | - | https://www.conrad.de/de/p/fenix-are-c2-rundzellen-ladegeraet-nicd-nimh-liion-10440-14500-16340-18650-26650-micro-aaa-mignon-aa-baby-1205975.html | 42
 | SUM exklusive MwSt |  |  | 143.45 |  | 112.07 |  | 160.65 |  | 456.62
 | SUM inklusive MwSt |  |  | 170.7055 |  | 133.3633 |  | 191.1735 |  | 543.3778

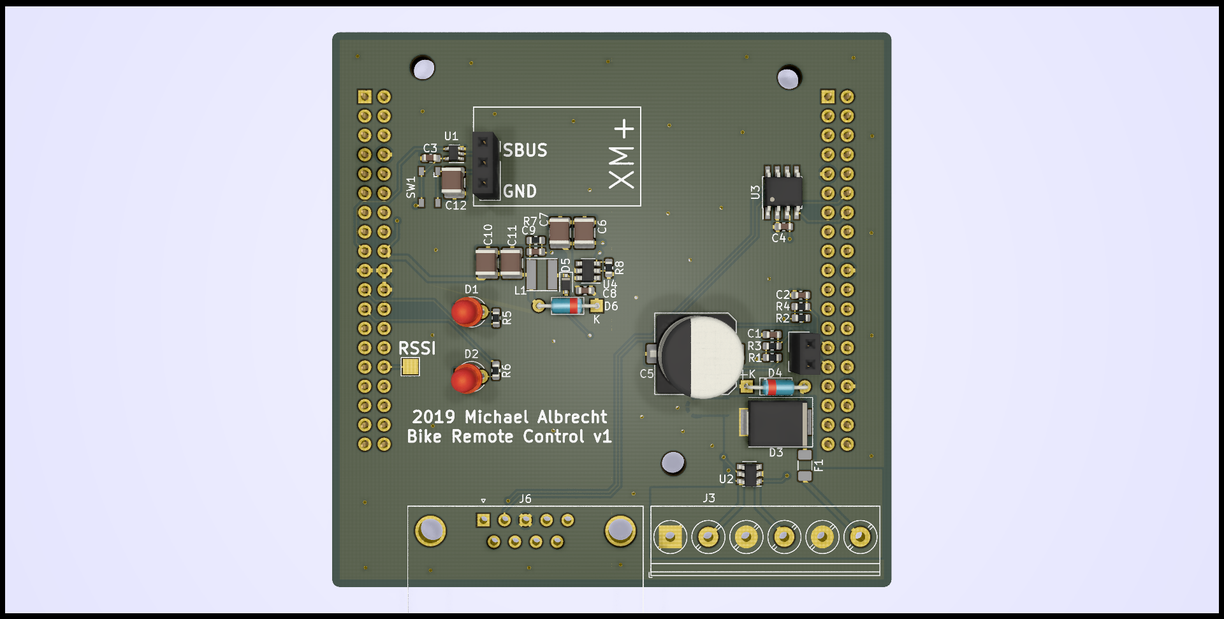
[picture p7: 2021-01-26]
hardware/firstCompleteLayout.png

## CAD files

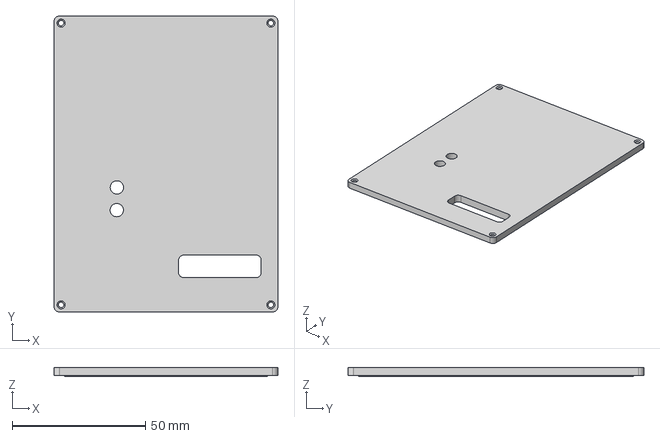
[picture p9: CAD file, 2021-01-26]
hardware/3D/Housing - case top v1.step
84.0 x 111.0 x 3.50 mm

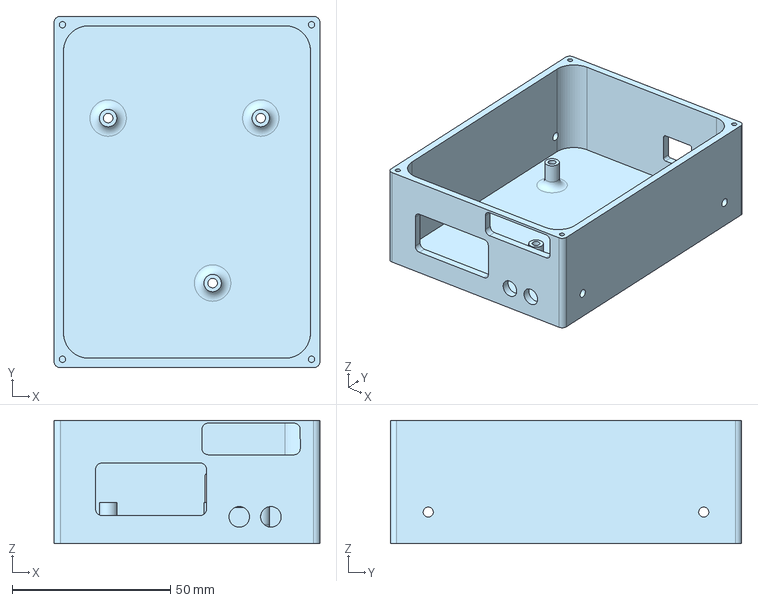
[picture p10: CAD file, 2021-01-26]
hardware/3D/Housing - case bottom v1.step
84.0 x 111.0 x 39.0 mm

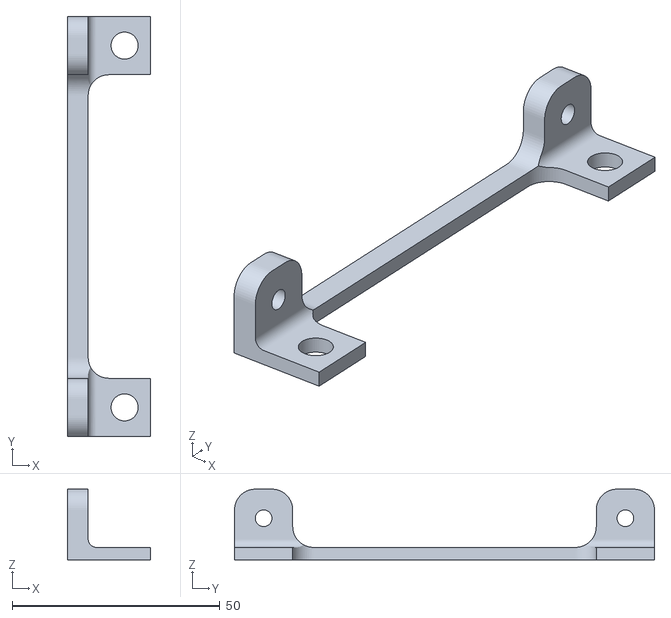
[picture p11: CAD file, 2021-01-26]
hardware/3D/Housing fastening Adapter - housing fastening adapter.stl
20.0 x 101.0 x 17.0

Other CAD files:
hardware/3D/Housing - case bottom v1.stl
hardware/3D/Housing - case top v1.stl

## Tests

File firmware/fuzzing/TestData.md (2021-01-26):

#### File Format
Everything is in binary without spacers. XML syntax is only used for clarification.

```
<Instruction><Type size=1 /><Payload size=* /></Instruction><Instruction>...
```

- Instruction *0x0* Modifies RCSwitchState and HardwareSwitchState.
  - **Payload**
  - Index 0: States (One bit for State). See main.cpp for bit meanings.
- Instruction *0x1* "Sends" a can frame to the stack. Currently everything **not** 0x0 is interpreted as 0x1.
  - **Playload** 
  - Index 0: Data Length (0-8 bytes) 
  - Index 1: RTR Flag (0 for no, else for yes)
  - Index 2: High Byte of CanId
  - Index 3: Low Byte of CanId
  - (Index 4 - 12: Frame data, starting with highest byte)

#### goodTestData.bin Interpretation 

```cpp
# sw: neutral rc: timeout=true switches neutral 
00  40 
# can: some pdos unrelated to programm
01  04  00  0190 00110022
01  00  01  0250
01  08  00  03ff 0011223344556677
# can: rtd status bootup
01  01  00  0182 00
# -> to state: startup 

# sw: neutral rc: timeout=false switches neutral 
00  00
# can: rtd status ready
01  01  00  0182 01
# can: monitored devices bootup
01  01  00  0710  05
01  01  00  0720  05
01  01  00  0721  05
01  01  00  0730  05
01  01  00  0731  05
# -> to state: idle

# sw: neutral rc: timeout=false unlock, remote switch
00  4C
# -> to state: remote

# sw: neutral rc: timeout=false unlock, autonomous switch
00  5C
# -> to state: autonomous

# sw: neutral rc: timeout=false, button emcy
00  20
# -> to state: softemcy

# sw: manual rc: timeout=true
00  41
# -> to state: manual

# can: rtd status emcy
01  01  00  0182 05

# sw: bikeemcy rc: timeout=true
00  42
# -> to state: hardemcy
```

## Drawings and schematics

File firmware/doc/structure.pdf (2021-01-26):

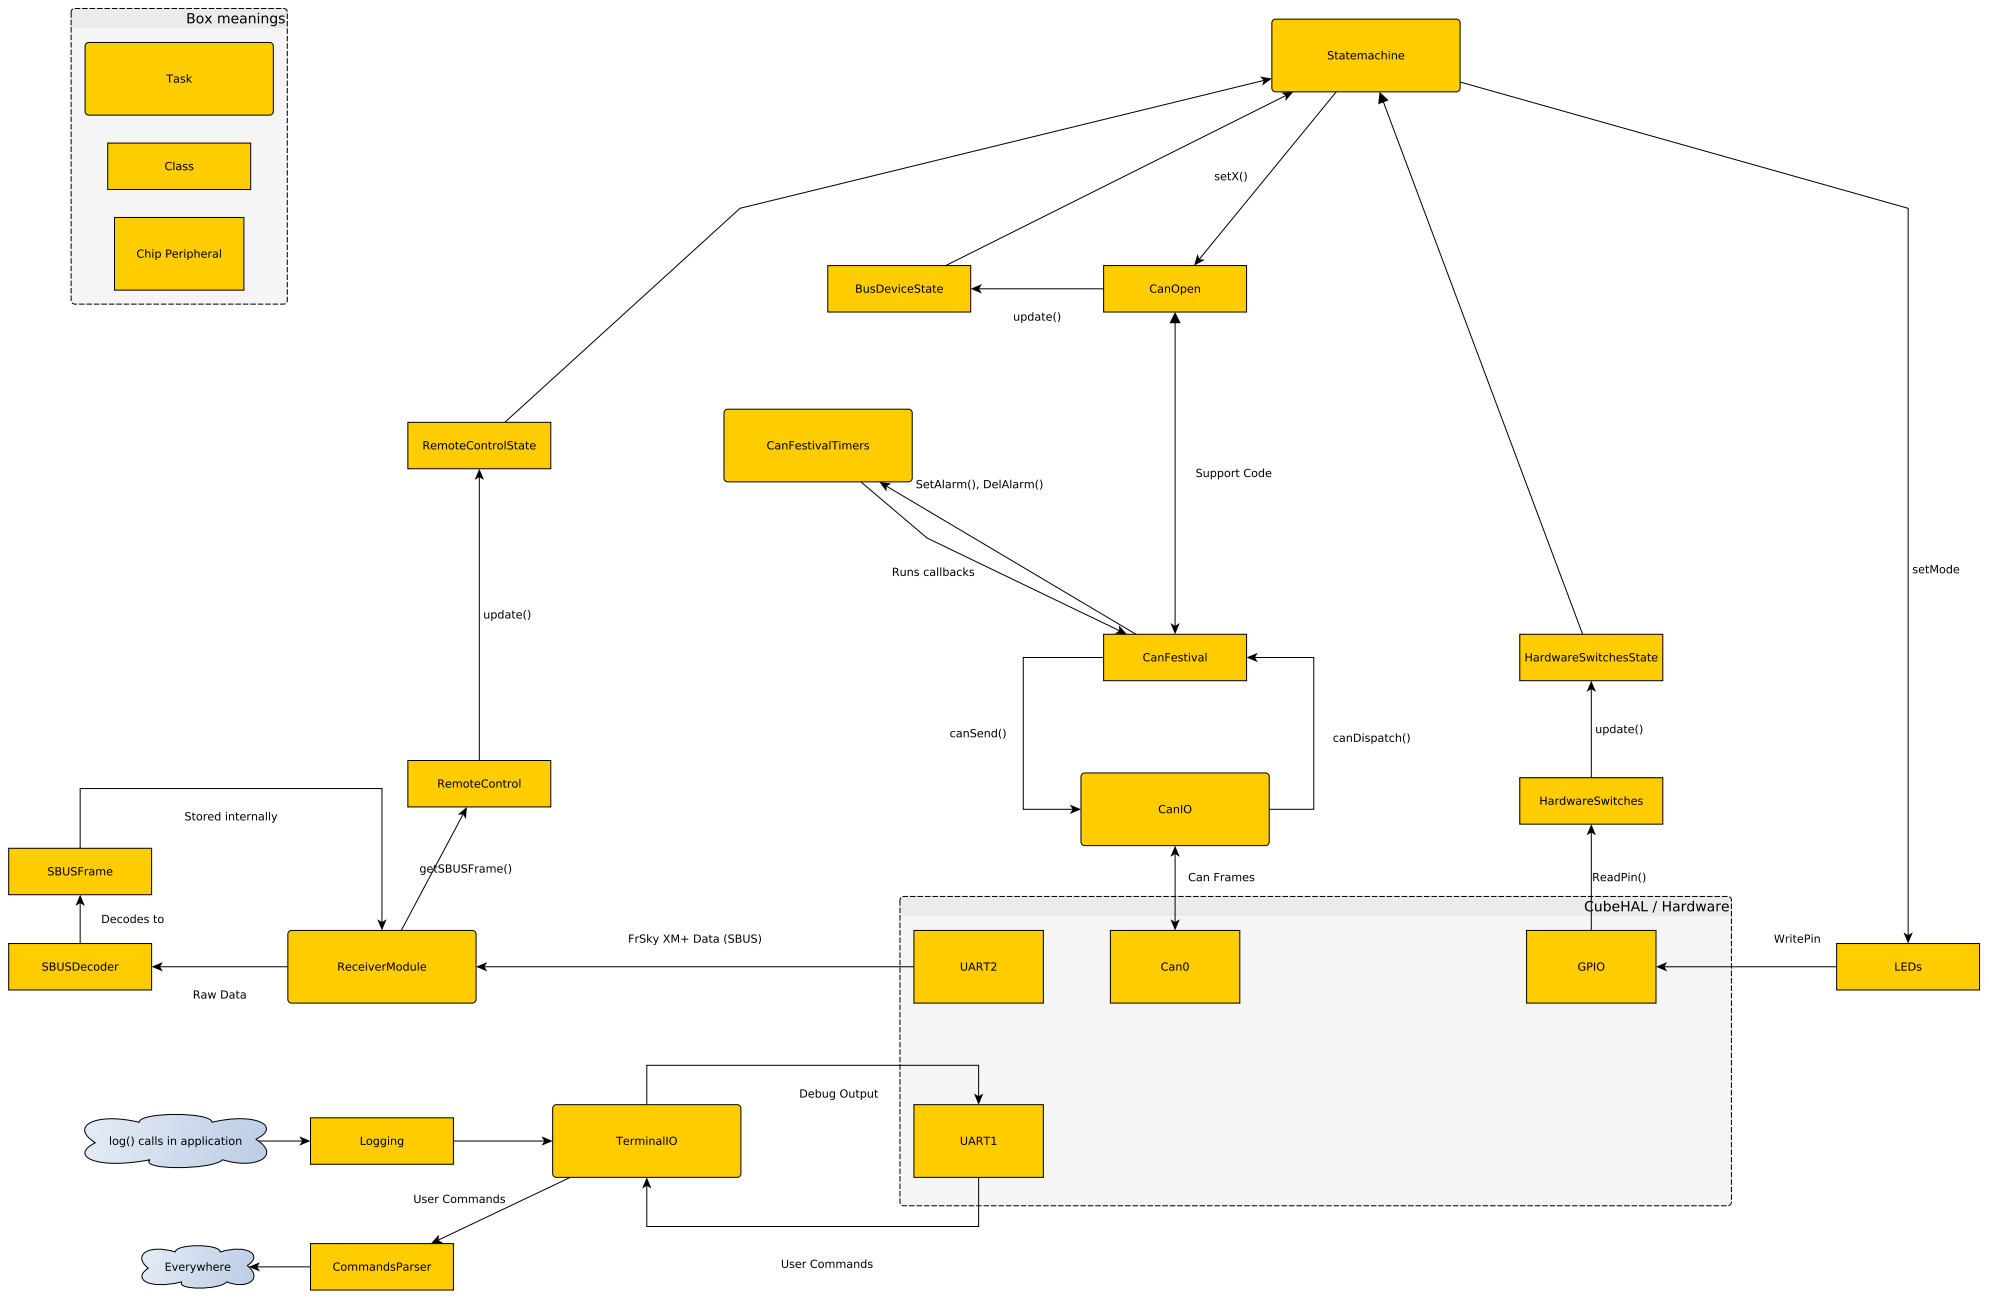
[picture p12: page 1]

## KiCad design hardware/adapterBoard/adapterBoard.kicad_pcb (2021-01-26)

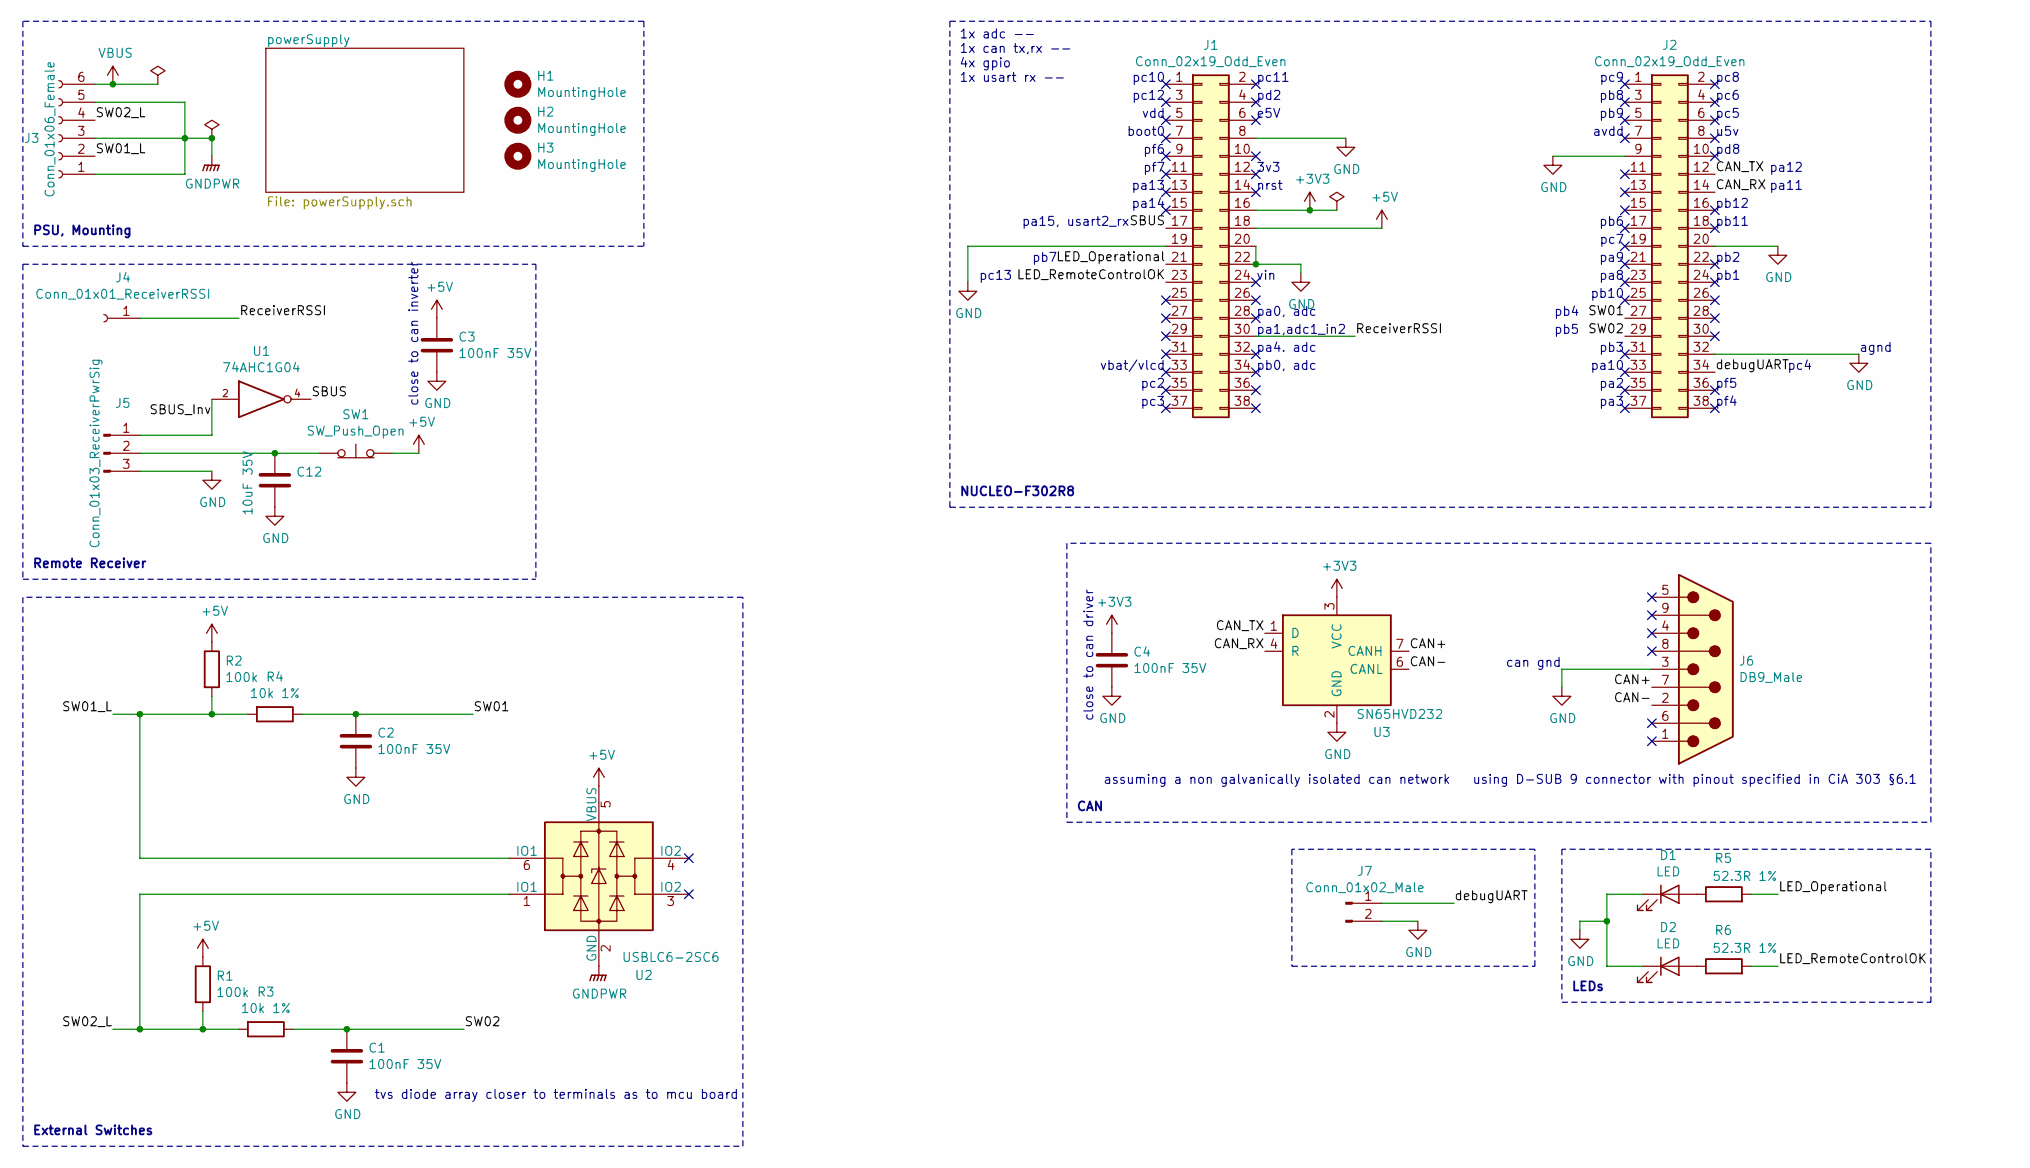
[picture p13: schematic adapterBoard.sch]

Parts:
C1, C2, C3, C4: 100nF 35V; C_0603_1608Metric
C12: 10uF 35V; C_1210_3225Metric
D1, D2: LED; LED_D3.0mm
H1, H2, H3: MountingHole; MountingHole_3mm
J1, J2: Conn_02x19_Odd_Even; PinSocket_2x19_P2.54mm_Vertical
J3: Conn_01x06_Female; TerminalBlock_Phoenix_PT-1,5-6-5.0-H_1x06_P5.00mm_Horizontal
J4: Conn_01x01_ReceiverRSSI; TestPoint_Pad_2.0x2.0mm
J5: Conn_01x03_ReceiverPwrSig; PinSocket_1x03_P2.54mm_Vertical
J6: DB9_Male; DSUB-9_Male_Horizontal_P2.77x2.84mm_EdgePinOffset9.90mm_Hou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
J7: Conn_01x02_Male; PinSocket_1x02_P2.54mm_Vertical
R1, R2: 100k; R_0603_1608Metric
R3, R4: 10k 1%; R_0603_1608Metric
R5, R6: 52.3R 1%; R_0603_1608Metric
SW1: SW_Push_Open; alps_SKRPASE010
U1: 74AHC1G04; SOT-353_SC-70-5
U2: USBLC6-2SC6; SOT-23-6
U3: SN65HVD232; SOIC-8_3.9x4.9mm_P1.27mm

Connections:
+3V3: C4.1, J1.16, U3.3 (VCC)
+5V: C3.1, J1.18, R1.1, R2.1, SW1.2 (B), U1.5 (VCC), U2.5 (VBUS); also elsewhere on the board
/CAN+: J6.7, U3.7 (CANH)
/CAN-: J6.2, U3.6 (CANL)
/CAN_RX: J2.14, U3.4 (R)
/CAN_TX: J2.12, U3.1 (D)
/LED_Operational: J1.21, R5.2
/LED_RemoteControlOK: J1.23, R6.2
/ReceiverRSSI: J1.30, J4.1
/SBUS: J1.17, U1.4
/SBUS_Inv: J5.1, U1.2
/SW01: C2.1, J2.27, R4.1
/SW01_L: J3.2, R2.2, R4.2, U2.6 (IO1)
/SW02: C1.1, J2.29, R3.1
/SW02_L: J3.4, R1.2, R3.2, U2.1 (IO1)
/debugUART: J2.34, J7.1
GND: C1.2, C2.2, C3.2, C4.2, C12.2, D1.1 (K), D2.1 (K), J1.8, J1.19, J1.20, J1.22, J2.9, J2.20, J2.32, J5.3, J6.3, J7.2, U1.3 (GND), U3.2 (GND); also elsewhere on the board
GNDPWR: J3.1, J3.3, J3.5, U2.2 (GND); also elsewhere on the board
unnamed: C12.1, J5.2, SW1.1 (A)
unnamed: D1.2 (A), R5.1
unnamed: D2.2 (A), R6.1
VBUS: J3.6; also elsewhere on the board

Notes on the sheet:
vdd
boot0
vbat/vlcd
e5V
close to can driver
tvs diode array closer to terminals as to mcu board
assuming a non galvanically isolated can network
using D-SUB 9 connector with pinout specified in CiA 303 §6.1
can gnd
NUCLEO-F302R8
CAN
LEDs
Remote Receiver
PSU, Mounting
External Switches
close to can inverter
1x adc -- 1x can tx,rx -- 4x gpio 1x usart rx --
nrst
3v3
vin
pc4
pa15, usart2_rx
pc10
pc12
pf6
pf7
pa13
pa14
pb7
pc13
pc2
pc3
pc11
pd2
pa0, adc
pa1,adc1_in2
pa4. adc
pb0, adc
pc9
pb8

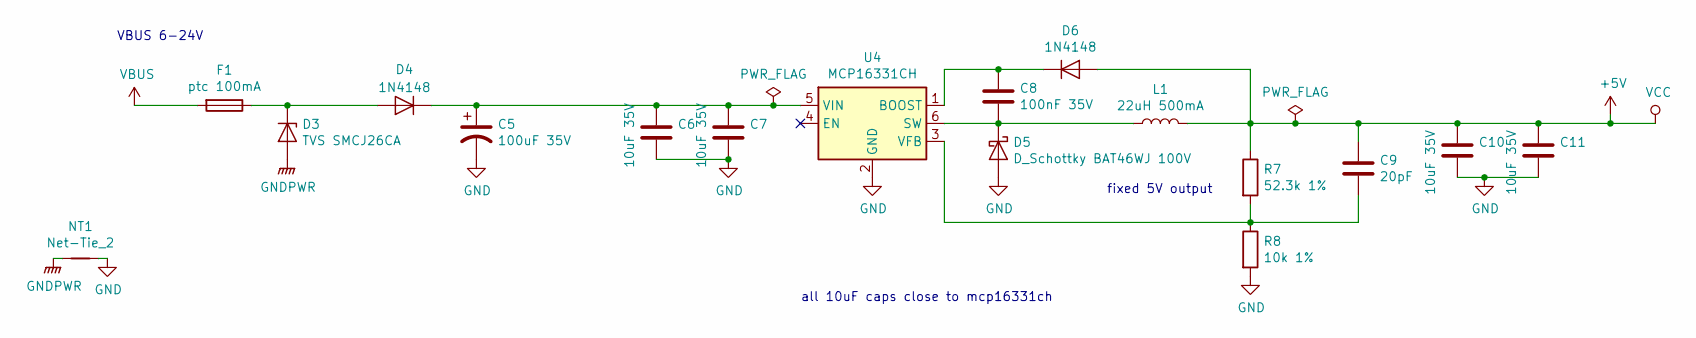
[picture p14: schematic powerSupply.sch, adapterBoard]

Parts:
C5: 100uF 35V; CP_Elec_10x10.5
C6, C7, C10, C11: 10uF 35V; C_1210_3225Metric
C8: 100nF 35V; C_0603_1608Metric
C9: 20pF; C_0603_1608Metric
D3: TVS SMCJ26CA; D_SMC
D4, D6: 1N4148; D_DO-35_SOD27_P7.62mm_Horizontal
D5: D_Schottky BAT46WJ 100V; D_SOD-323F
F1: ptc 100mA; Fuse_1206_3216Metric
L1: 22uH 500mA; L_Taiyo-Yuden_NR-40xx
NT1: Net-Tie_2; NetTie-2_SMD_Pad2.0mm
R7: 52.3k 1%; R_0603_1608Metric
R8: 10k 1%; R_0603_1608Metric
U4: MCP16331CH; SOT-23-6

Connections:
+5V: C9.1, C10.1, C11.1, D6.2 (A), L1.2, R7.1; also elsewhere on the board
GND: C5.2, C6.2, C7.2, C10.2, C11.2, D5.2 (A), NT1.2, R8.2, U4.2 (GND); also elsewhere on the board
GNDPWR: D3.2 (A), NT1.1; also elsewhere on the board
unnamed: C5.1, C6.1, C7.1, D4.1 (K), U4.5 (VIN)
unnamed: C8.1, D6.1 (K), U4.1 (BOOST)
unnamed: C8.2, D5.1 (K), L1.1, U4.6 (SW)
unnamed: C9.2, R7.2, R8.1, U4.3 (VFB)
unnamed: D3.1 (K), D4.2 (A), F1.1
VBUS: F1.2; also elsewhere on the board

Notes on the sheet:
fixed 5V output
all 10uF caps close to mcp16331ch
VBUS 6-24V

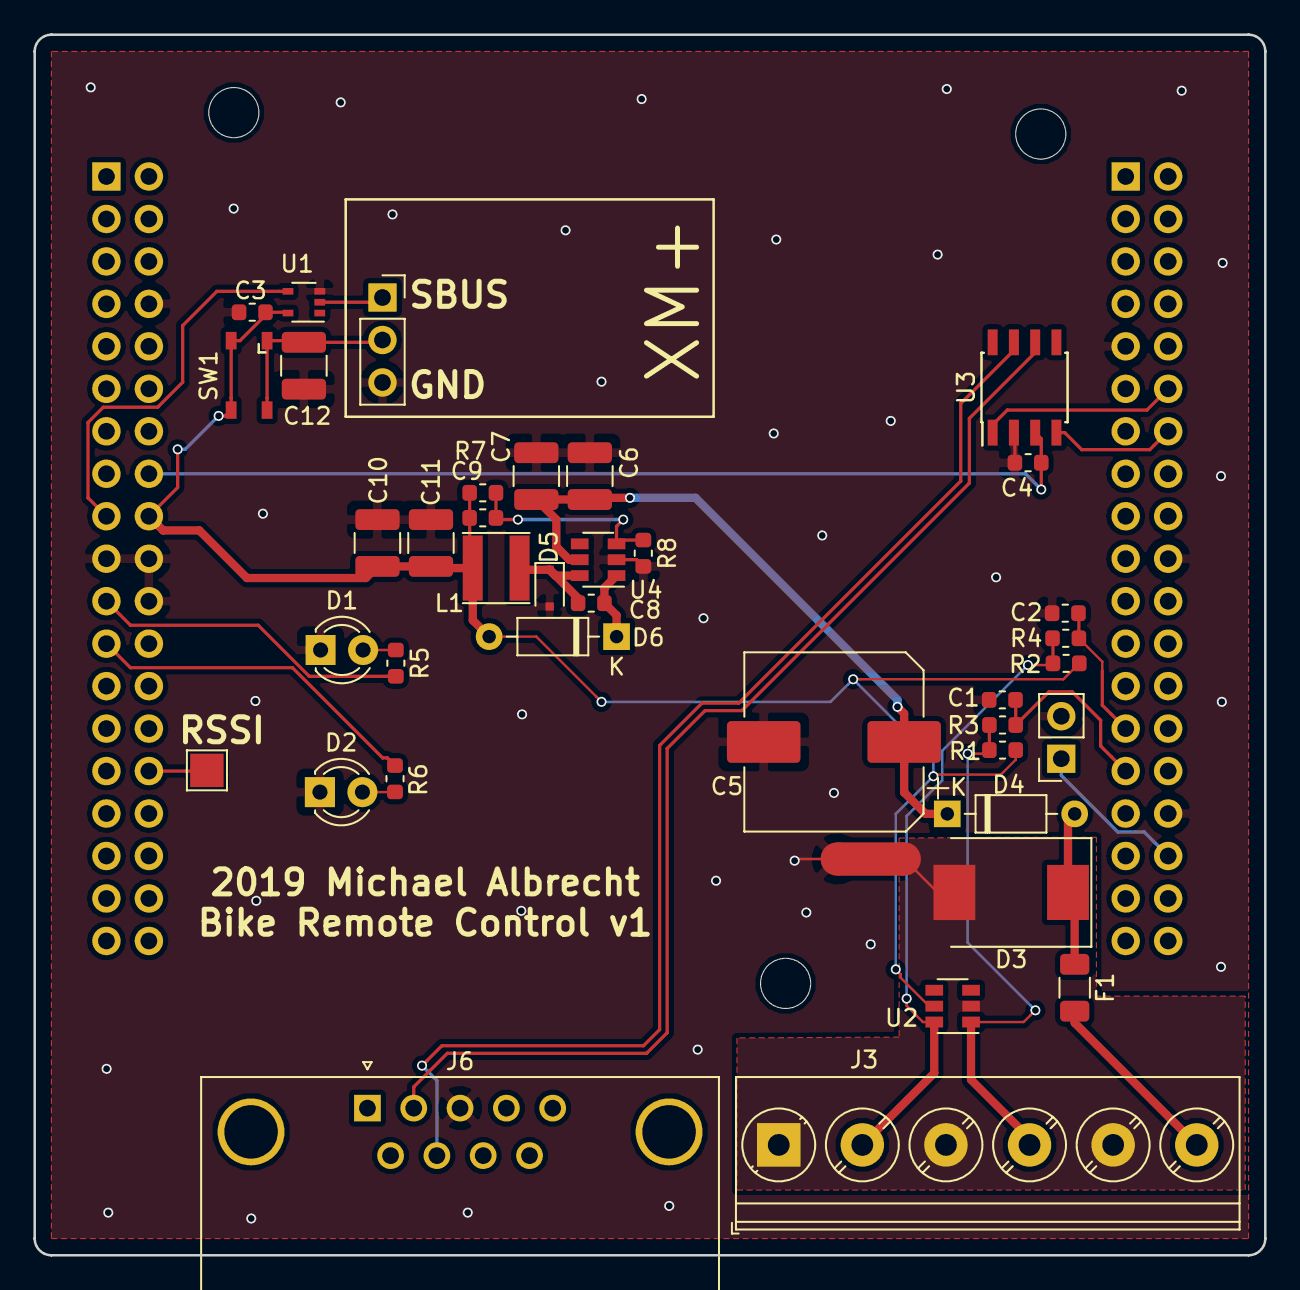
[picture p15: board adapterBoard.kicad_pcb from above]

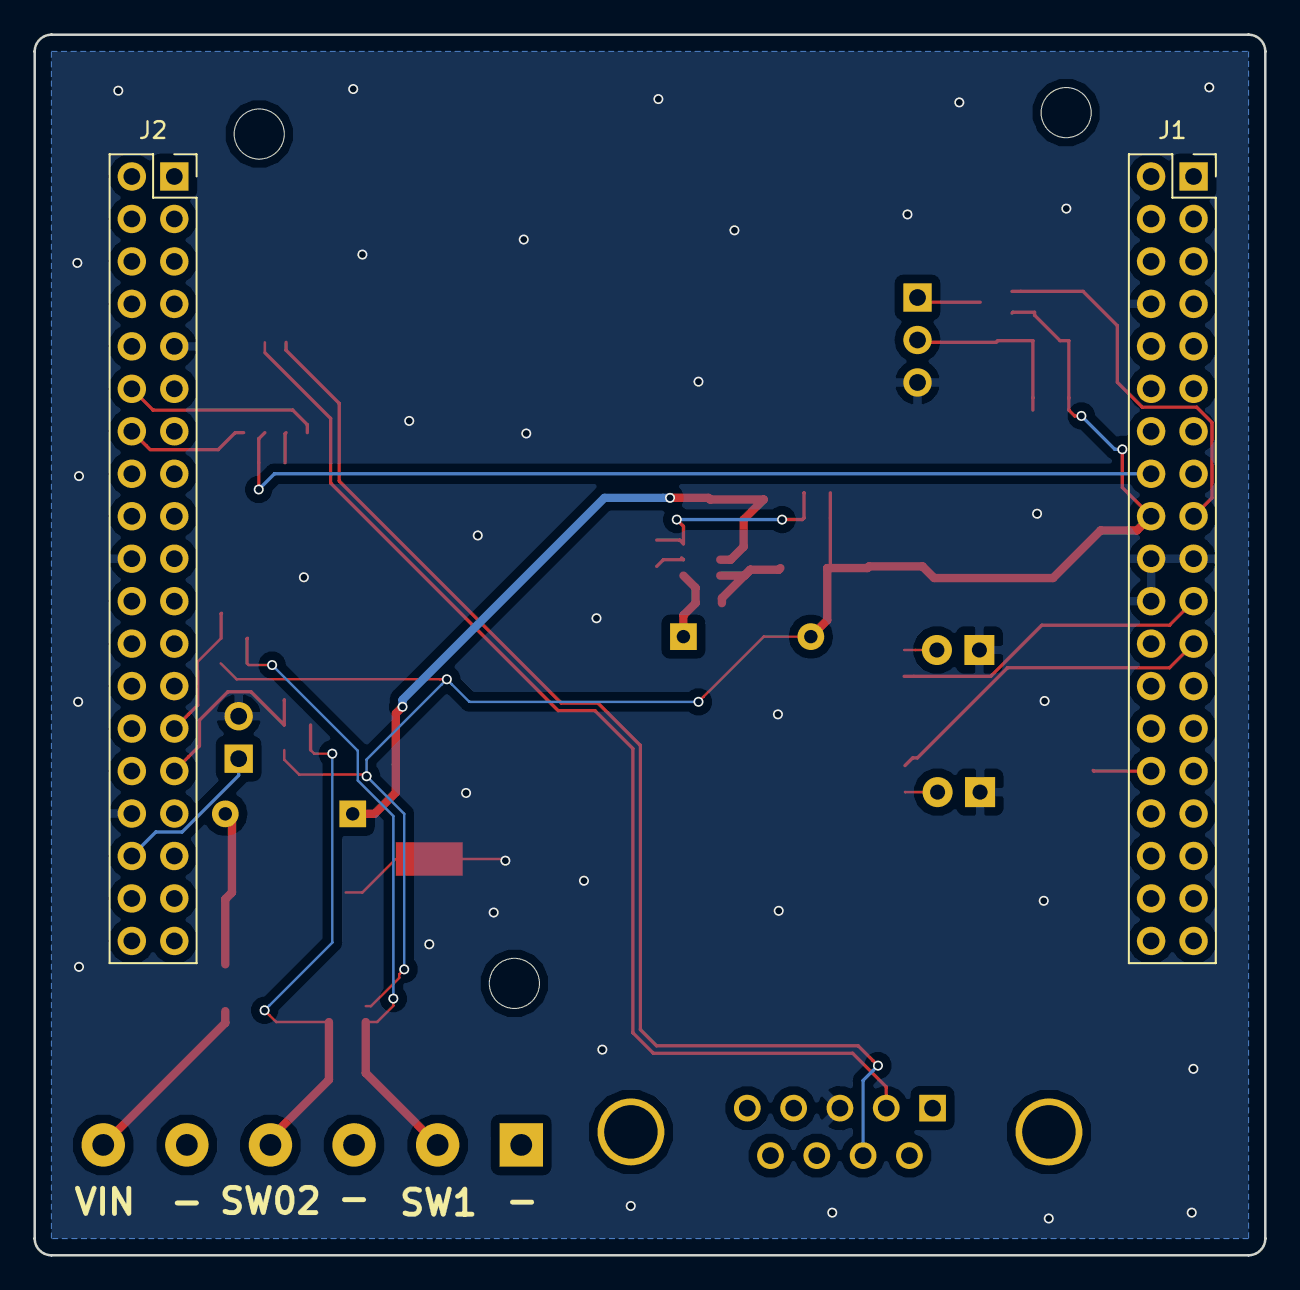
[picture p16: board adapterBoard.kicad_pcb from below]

Board: 2 copper layers, 73.6 x 73.0 mm, 44 parts (2 on the bottom side), 27 nets.

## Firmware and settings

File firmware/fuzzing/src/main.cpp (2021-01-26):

#include <array>
#include <exception>
#include <iostream>

#include <CEncapsulation/HAL.hpp>
#include <CanFestival/CanFestivalLocker.hpp>
#include <CanFestival/CanFestivalTimers.hpp>
#include <FreeRTOS.h>
#include <LEDs.hpp>
#include <PeripheralDrivers/CanIO.hpp>
#include <Statemachine/Canopen.hpp>
#include <Statemachine/HardwareSwitches.hpp>
#include <Statemachine/LEDUpdater.hpp>
#include <Statemachine/RemoteControl.hpp>
#include <Statemachine/StateSources.hpp>
#include <Statemachine/Statemachine.hpp>
#include <fake/Task.hpp>
#include <fstream>
#include <vector>

using namespace remote_control_device;

class RemoteControl_FileControlled : public RemoteControl
{
public:
    RemoteControl_FileControlled(RemoteControlState &target) : target(target)
    {
    }
    virtual ~RemoteControl_FileControlled() = default;
    virtual void update(RemoteControlState &trgt) const final
    {
        trgt = target;
    }

private:
    RemoteControlState &target;
};

class HardwareSwitches_FileControlled : public HardwareSwitches
{
public:
    HardwareSwitches_FileControlled(HardwareSwitchesState &target) : target(target)
    {
    }
    virtual ~HardwareSwitches_FileControlled() = default;
    virtual void update(HardwareSwitchesState &state) const final
    {
        state = target;
    }

private:
    HardwareSwitchesState &target;
};

class MyException : public std::runtime_error
{
public:
    MyException() : std::runtime_error("")
    {
    }
};

int main(int argc, char *argv[])
{
    if (argc == 2)
    {
        // printf("The argument supplied is %s\n", argv[1]);
    }
    else if (argc > 2)
    {
        printf("Too many arguments supplied.\n");
        return 0;
    }
    else
    {
        printf("One argument expected.\n");
        return 0;
    }

    // file content sets hardware and rc switches
    // pulled from here
    HardwareSwitchesState hwSwitchesState;
    RemoteControlState rcState;

    // Startup application
    FakeTaskContainer task;

    CanIO canio(task.get(), nullptr);
    LED ledRc(nullptr, 0, nullptr);
    LED ledHw(nullptr, 0, nullptr);
    LEDUpdater ledU(ledHw, ledRc, canio);
    HAL hal;
    CanFestivalTimers cft(hal);
    Canopen co;
    HardwareSwitches_FileControlled hws(hwSwitchesState);
    RemoteControl_FileControlled rc(rcState);
    Statemachine sm(co, rc, hws, ledU);

    // open file, read content
    std::ifstream f(argv[1], std::ifstream::in | std::ifstream::binary);
    size_t filesize = 0;
    if (!f) {
        return -1;
    }

    f.seekg(0, std::ios::end);
    filesize = f.tellg();
    f.seekg(0, std::ios::beg);
    char *data = nullptr;

    if (filesize > 0)
    {
        data = new char[filesize];
        f.read(data, filesize);
    }

    // dispatch once with default values
    sm.dispatch();
    cft.dispatch();

    // parse file and execute what is in it
    auto checkIndex = [&](size_t index) -> void {
        if (index >= filesize)
        {
            throw MyException();
        }
    };
    try
    {
        for (size_t i = 0; i < filesize; ++i)
        {
            //std::cout<<"\t offset: "<<i<<"\n";
            if (data[i] == 0)
            {
                // rc, hardware state change
                checkIndex(++i);
                char state = data[i];
                hwSwitchesState.ManualSwitch = (state & (1 << 0)) > 0;
                hwSwitchesState.BikeEmergency = (state & (1 << 1)) > 0;
                rcState.switchUnlock = (state & (1 << 2)) > 0;
                rcState.switchRemoteControl = (state & (1 << 3)) > 0;
                rcState.switchAutonomous = (state & (1 << 4)) > 0;
                rcState.buttonEmergency = (state & (1 << 5)) > 0;
                rcState.timeout = (state & (1 << 6)) > 0;
                //std::cout<<"rc update\n";
            }
            else if (data[i] > 0)
            {
                // can frame
                Message m = Message_Initializer;

                // length
                checkIndex(++i);
                m.len = data[i];
                if (m.len > 8)
                {
                    continue;
                }

                // rtr
                checkIndex(++i);
                m.rtr = data[i] > 0 ? 1 : 0;

                // canId
                // file is created by hand so everything is big endian
                checkIndex(++i);
                m.cob_id = static_cast<UNS16>(data[i]) << 8;
                checkIndex(++i);
                m.cob_id |= static_cast<UNS16>(data[i]);

                // extract data
                if (m.len > 0)
                {
                    for (int j = m.len - 1; j >= 0; --j)
                    {
                        checkIndex(++i);
                        m.data[j] = data[i];
                    }
                }
                CFLocker locker;
                canDispatch(locker.getOD(), &m);
                //std::cout<<"can update\n";
            } else {
                //std::cout<<"unknown \n";
                return -1;
            }

            // calls HardwareSwitches_FileControlled.update (+rc_filecontrolled.update)
            // which will grab our modified states
            sm.dispatch();
            cft.dispatch();
        }
    }
    catch (const MyException &myEx)
    {
        // no worries, expected exception
        // fuzzer does all kinds of crazy things with the file so anything goes
    }

    if (data)
    {
        delete[] data;
    }
    //std::cout<<"all done :)\n";
    return 0;
}

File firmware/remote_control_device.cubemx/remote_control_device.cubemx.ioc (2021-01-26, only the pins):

Mcu.UserName=STM32F302R8Tx
PA11.Signal=CAN_RX
PA12.Signal=CAN_TX
PA13.GPIO_Label=TMS
PA13.Signal=SYS_JTMS-SWDIO
PA14.GPIO_Label=TCK
PA14.Signal=SYS_JTCK-SWCLK
PA15.GPIO_Label=USART_RX
PA15.Signal=USART2_RX
PA2.GPIO_Label=USART_TX
PA2.Signal=USART2_TX
PB13.GPIO_Label=LD2 [Green Led]
PB13.Signal=GPIO_Output
PB3.GPIO_Label=SWO
PB3.Signal=SYS_JTDO-TRACESWO
PB4.GPIO_Label=hardwareSwitch1
PB4.Signal=GPIO_Input
PB5.GPIO_Label=hardwareSwitch2
PB5.Signal=GPIO_Input
PB7.GPIO_Label=ledHardware
PB7.Signal=GPIO_Output
PC13.GPIO_Label=ledRemote
PC13.Signal=GPIO_Output
PC4.Signal=USART1_TX
PC5.Signal=USART1_RX
PF0-OSC_IN.Signal=RCC_OSC_IN
PF1-OSC_OUT.Signal=RCC_OSC_OUT

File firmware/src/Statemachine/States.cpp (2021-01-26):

#include "States.hpp"
#include "Statemachine/Canopen.hpp"
#include "Statemachine/StateSources.hpp"
#include "Statemachine/Statemachine.hpp"

namespace remote_control_device
{

States::States()
    : // clang-format off
_states{{ 
        /* Start */
        State(
            /* id */ StateId::Start,
            /* priority */ 255,

            /* brake coupling */ CouplingState::Disengaged,
            /* steering coupling */ CouplingState::Disengaged,

            /* send targets */ false,
            /* steering status */ CanDeviceState::Operational, 
            /* brake status */ CanDeviceState::Operational,
            /* drive motor status */ CanDeviceState::Operational,

            /* requires unlock */ false,

            new StateCallbacks(
                /* process function*/
                [](StateChaningSources &src) -> void {
                    // not starting up until all devices are online and 
                    // rtd_state signals sucessful bootup
                    if (src.busDevicesState.rtdBootedUp && !src.busDevicesState.timeout) 
                    { 
                        src.sigalStartedUp();
                    }
                },
                /* check conditions */
                [](StateChaningSources &src) -> bool { 
                    return !src.isStartedUp(); 
                },
                /* one time setup */ 
                [](StateChaningSources &src) -> void { 
                }
            )
        ),

        /* Idle */
        State(
            /* id */ StateId::Idle,
            /* priority */ IDLE_STATE_PRIORITY,

            /* brake coupling */ CouplingState::Disengaged,
            /* steering coupling */ CouplingState::Disengaged,

            /* send targets */ false,
            /* steering status */ CanDeviceState::Preoperational,
            /* brake status */ CanDeviceState::Operational,
            /* drive motor status */ CanDeviceState::Operational,
            
            /* requires unlock */ false,

            new StateCallbacks(
                /* process function*/
                [](StateChaningSources &src) -> void {
                    return;
                },
                /* check conditions */
                [](StateChaningSources &src) -> bool { 
                    return true; // gets replaced anyways
                },
                /* one time setup */ 
                [](StateChaningSources &src) -> void {
                    // reset brake, motor torque just once with enable->disable 
                    // see canopen:: setActuatorPDOs and kickstartPDOTransmission
                    src.canopen.setWheelDriveTorque(0);
                    src.canopen.setBrakeForce(0);
                    src.canopen.setActuatorPDOs(true);
                    src.canopen.setActuatorPDOs(false);
                }
            )
        ),

        /* RemoteControl */
        State(
            /* id */ StateId::RemoteControl,
            /* priority */ 11,

            /* brake coupling */ CouplingState::Engaged,
            /* steering coupling */ CouplingState::Engaged,

            /* send targets */ true,
            /* steering status */ CanDeviceState::Operational,
            /* brake status */ CanDeviceState::Operational,
            /* drive motor status */ CanDeviceState::Operational,

            /* requires unlock */ true,

            new StateCallbacks(
                /* process function*/
                [](StateChaningSources &src) -> void {
                    src.canopen.setBrakeForce(src.remoteControl.brake);
                    src.canopen.setWheelDriveTorque(src.remoteControl.throttle);
                    src.canopen.setSteeringAngle(src.remoteControl.steering);
                    return;
                },
                /* check conditions */
                [](StateChaningSources &src) -> bool { 
                    return  src.remoteControl.switchRemoteControl && (!src.remoteControl.switchAutonomous) && (!src.remoteControl.throttleIsUp);
                },
                /* one time setup */ 
                [](StateChaningSources &src) -> void { 
                }
            )
        ),

        /* Autonomous */
        State(
            /* id */ StateId::Autonomous,
            /* priority */ 10,

            /* brake coupling */ CouplingState::Engaged,
            /* steering coupling */ CouplingState::Engaged,

            /* send targets */ false,
            /* steering status */ CanDeviceState::Operational,
            /* brake status */ CanDeviceState::Operational,
            /* drive motor status */ CanDeviceState::Operational,

            /* requires unlock */ true,

            new StateCallbacks(
                /* process function*/
                [](StateChaningSources &src) -> void {
                    return;
                },
                /* check conditions */
                [](StateChaningSources &src) -> bool { 
                    return  src.remoteControl.switchAutonomous && (!src.remoteControl.switchRemoteControl);
                },
                /* one time setup */ 
                [](StateChaningSources &src) -> void { 
                }
            )
        ),

        /* SoftEmergency */
        State(
            /* id */ StateId::SoftEmergency,
            /* priority */ 100,

            /* brake coupling */ CouplingState::Engaged,
            /* steering coupling */ CouplingState::Engaged,

            /* send targets */ true,
            /* steering status */ CanDeviceState::Operational,
            /* brake status */ CanDeviceState::Operational,
            /* drive motor status */ CanDeviceState::Operational,

            /* requires unlock */ false,

            new StateCallbacks(
                /* process function*/
                [](StateChaningSources &src) -> void {
                    src.canopen.setBrakeForce(Canopen::MaxBrakePressure);
                    src.canopen.setWheelDriveTorque(Canopen::NoWheelDriveTorque);
                    return;
                },
                /* check conditions */
                [](StateChaningSources &src) -> bool { 
                    // keep in emergency until all remote switches are back to 
                    // initial position
                    bool latchUp = src.currentState == StateId::SoftEmergency &&
                            (src.remoteControl.switchRemoteControl ||
                            src.remoteControl.switchAutonomous ||
                            src.remoteControl.switchUnlock);

                    return  src.remoteControl.timeout || 
                            src.remoteControl.buttonEmergency ||
                            src.busDevicesState.timeout ||
                            src.busDevicesState.rtdEmergency ||
                            latchUp;  
                },
                /* one time setup */ 
                [](StateChaningSources &src) -> void { 
                }
            )
        ),
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

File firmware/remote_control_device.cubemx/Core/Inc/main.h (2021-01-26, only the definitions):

#define ledRemote_Pin GPIO_PIN_13
#define ledRemote_GPIO_Port GPIOC
#define USART_TX_Pin GPIO_PIN_2
#define USART_TX_GPIO_Port GPIOA
#define LD2_Pin GPIO_PIN_13
#define LD2_GPIO_Port GPIOB
#define TMS_Pin GPIO_PIN_13
#define TMS_GPIO_Port GPIOA
#define TCK_Pin GPIO_PIN_14
#define TCK_GPIO_Port GPIOA
#define USART_RX_Pin GPIO_PIN_15
#define USART_RX_GPIO_Port GPIOA
#define SWO_Pin GPIO_PIN_3
#define SWO_GPIO_Port GPIOB
#define hardwareSwitch1_Pin GPIO_PIN_4
#define hardwareSwitch1_GPIO_Port GPIOB
#define hardwareSwitch2_Pin GPIO_PIN_5
#define hardwareSwitch2_GPIO_Port GPIOB
#define ledHardware_Pin GPIO_PIN_7
#define ledHardware_GPIO_Port GPIOB

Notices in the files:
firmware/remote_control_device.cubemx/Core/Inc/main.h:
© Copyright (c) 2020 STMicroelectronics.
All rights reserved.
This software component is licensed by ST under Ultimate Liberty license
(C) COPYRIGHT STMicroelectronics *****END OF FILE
